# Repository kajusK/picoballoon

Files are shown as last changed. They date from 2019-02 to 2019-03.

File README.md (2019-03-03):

Picoballoon challange 2019, team deadbadger probe
-------------------------------------------------

This repo contains source codes and hw design of the picoballoon probe designed
for https://www.hvezdarna.cz/?p=7694.

Due to the lack of free time, the pcb is very suboptimal as I needed single sided
board with wider traces for diy manufacturing process (made it few days before the
launch, didn't have enough time to send it to a pcb house).

The circuit contains:
- MCU stm32f070
- GPS u-blox max-m8
- Lora module HPD13
- Analog thermometer
- Digital pressure sensor MS5607 (failed to make it working before start - getting nack all the time)
- Solar panel that charges the supercap (wanted bare cells from china, but delivery time was too long, used one quite heavy panel from my junk box)
- 3.3 V boost switching power supply with startup circuit (starts around 2,5 V)

The software is quite simplified too. The Lmic library takes care of the LoRa
communications. Minmea handles processing nmea messages from gps. For future
reference, the libopencm3 is not the best option when dealing with stm32f0
family, I've had serious issues with rtc wakeup timer and failed
to wake up from deep sleep on rtc events anyway...

The code does following:
- Initialize peripherals
- Send LoRa join request
- Try to get the gps position
- After gps fix or timeout, send data over the LoRa connection and shutdown

Sending period depends on amount of sunlight (solar cell current) and supercap
capacity.

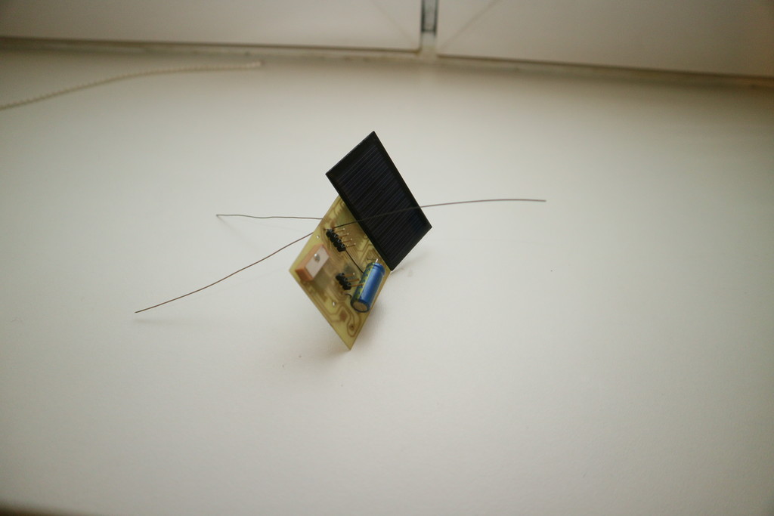
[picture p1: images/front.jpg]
Front

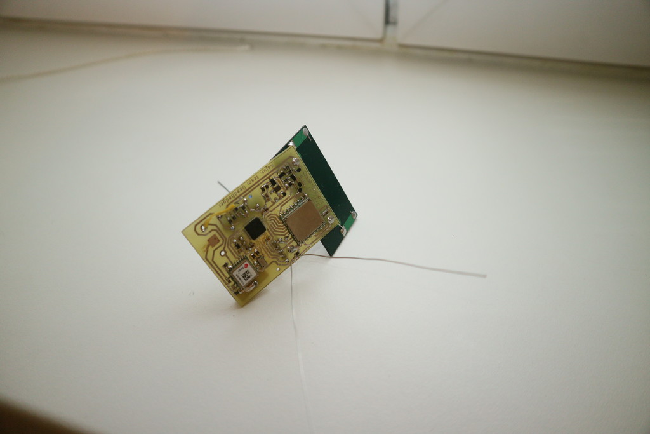
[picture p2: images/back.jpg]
Back


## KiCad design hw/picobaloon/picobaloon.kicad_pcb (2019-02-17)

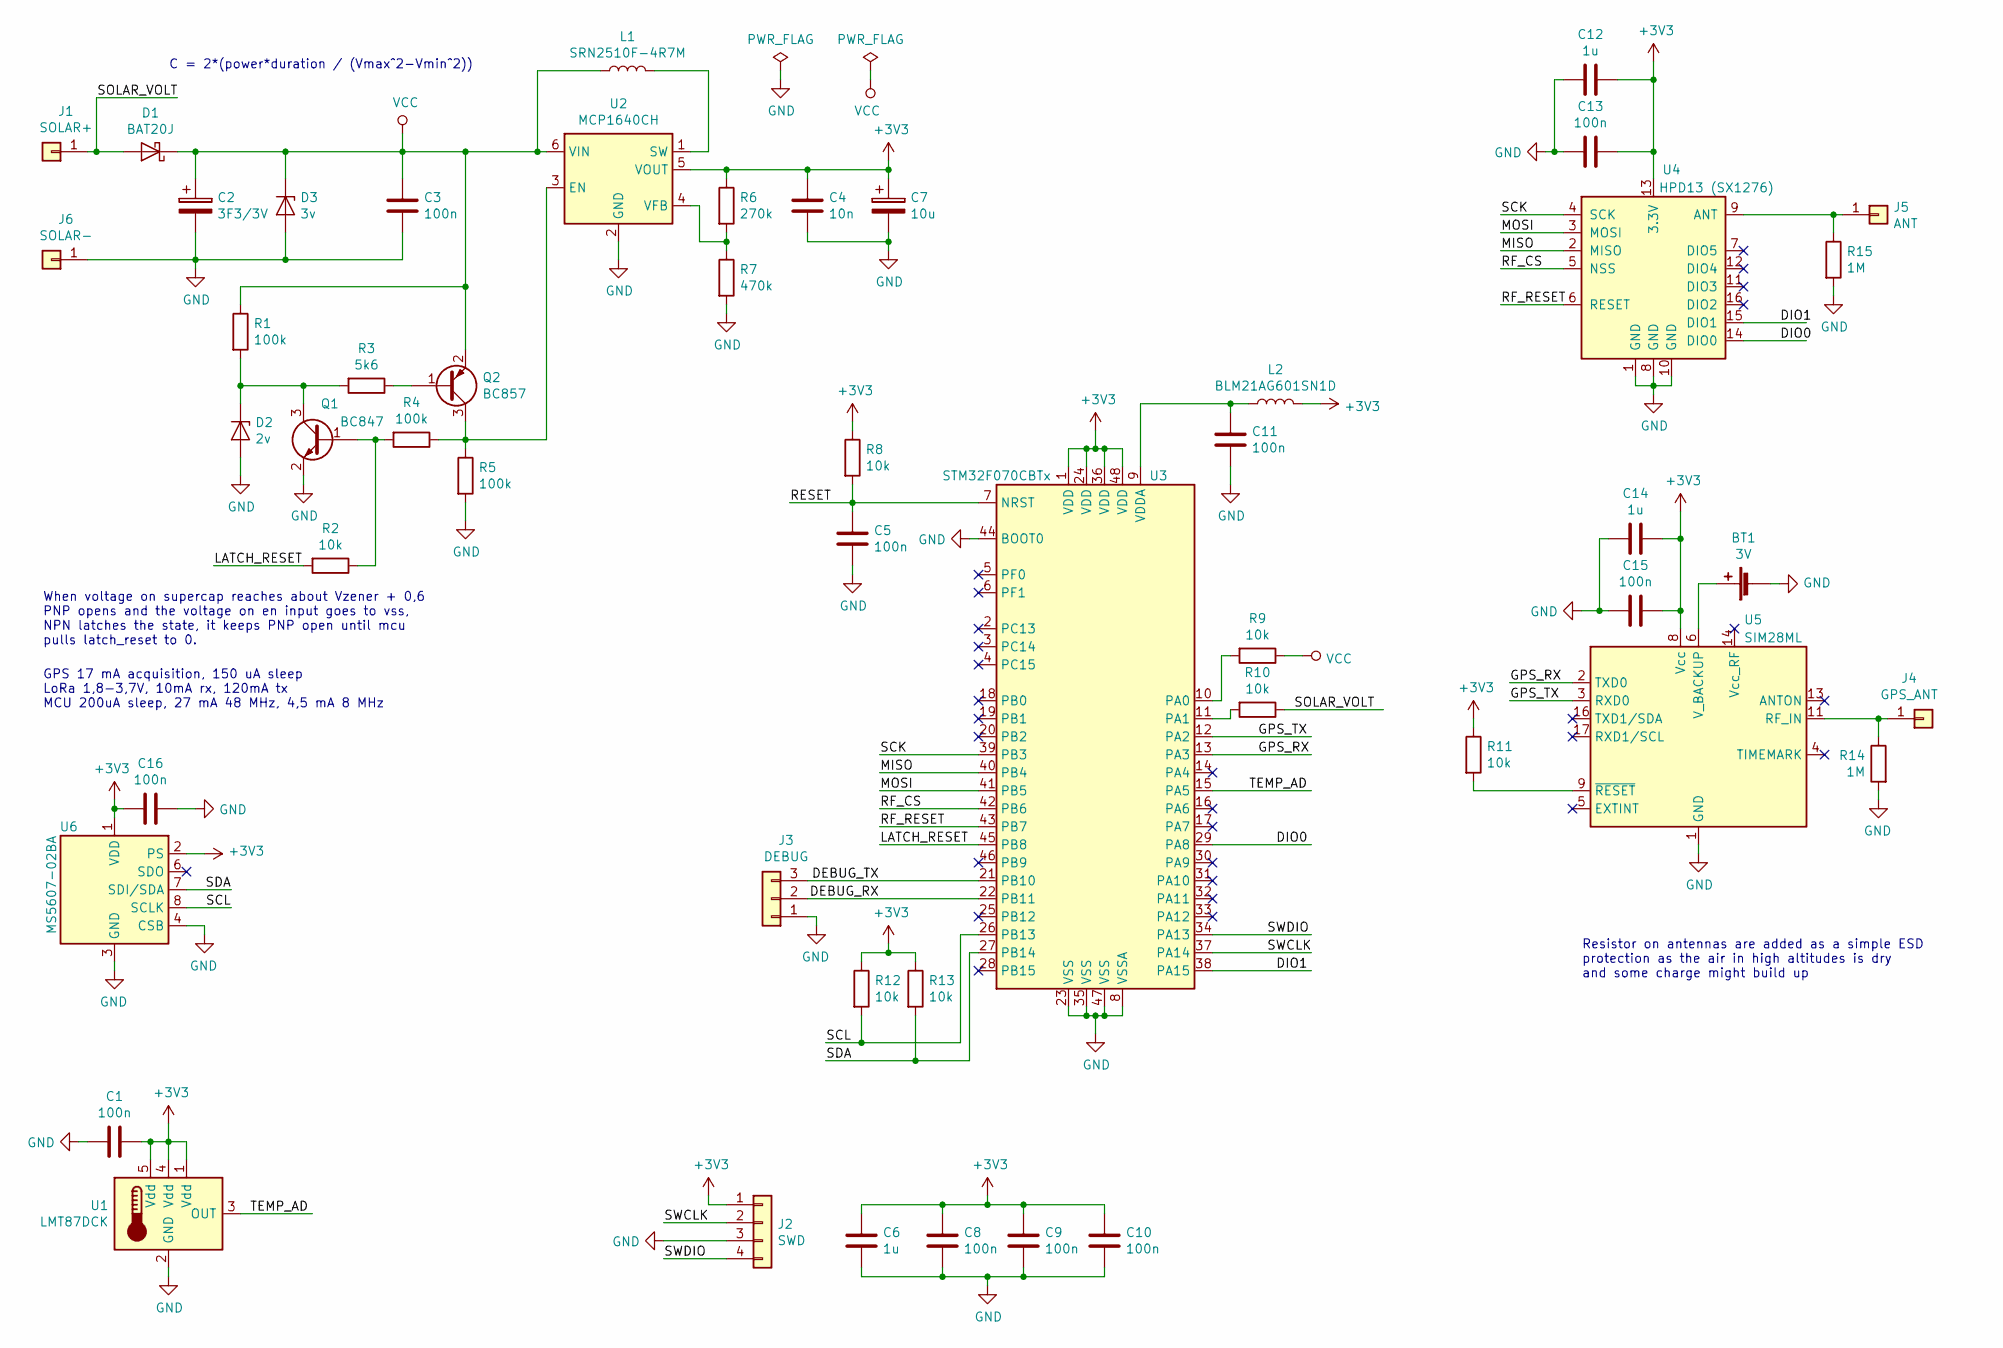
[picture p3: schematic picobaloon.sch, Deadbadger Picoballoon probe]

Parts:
BT1: 3V; BatteryHolder_Keystone_3001_1x12mm
C1, C3, C5, C8, C9, C10, C11, C13, C15, C16: 100n; C_0805_2012Metric
C2: 3F3/3V; CP_Radial_D8.0mm_P3.50mm
C4: 10n; C_0805_2012Metric
C6, C12, C14: 1u; C_0805_2012Metric
C7: 10u; C_0805_2012Metric
D1: BAT20J; D_SOD-323
D2: 2v; D_SOD-323
D3: 3v; D_SOD-323
J1: SOLAR+; SolderWirePad_1x01_Drill1.2mm
J2: SWD; PinHeader_1x04_P2.54mm_Vertical
J3: DEBUG; PinHeader_1x03_P2.54mm_Vertical
J4: GPS_ANT; SolderWirePad_1x01_Drill1.2mm
J5: ANT; SolderWirePad_1x01_Drill1.2mm
J6: SOLAR-; SolderWirePad_1x01_Drill1.2mm
L1: SRN2510F-4R7M; L_Abracon_ASPI-3012S
L2: BLM21AG601SN1D; L_0805_2012Metric
Q1: BC847; SOT-23
Q2: BC857; SOT-23
R1, R4, R5: 100k; R_0805_2012Metric
R2, R8, R9, R10, R11, R12, R13: 10k; R_0805_2012Metric
R3: 5k6; R_0805_2012Metric
R6: 270k; R_0805_2012Metric
R7: 470k; R_0805_2012Metric
R14, R15: 1M; R_0805_2012Metric
U1: LMT87DCK; SOT-353_SC-70-5
U2: MCP1640CH; SOT-23-6
U3: STM32F070CBTx; LQFP-48_7x7mm_P0.5mm
U4: HPD13 (SX1276); HOPERF_RFM9XW_SMD
U5: SIM28ML
U6: MS5607-02BA; LGA-8_3x5mm_P1.25mm

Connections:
+3V3: C1.1, C4.1, C6.1, C7.1, C8.1, C9.1, C10.1, C12.1, C13.1, C14.1, C15.1, C16.1, J2.1, L2.2, R6.1, R8.1, R11.1, R12.1, R13.1, U1.1 (Vdd), U1.4 (Vdd), U1.5 (Vdd), U2.5 (VOUT), U3.1 (VDD), U3.24 (VDD), U3.36 (VDD), U3.48 (VDD), U4.13 (3.3V), U5.8 (Vcc), U6.1 (VDD), U6.2 (PS)
/DEBUG_RX: J3.2, U3.22 (PB11)
/DEBUG_TX: J3.3, U3.21 (PB10)
/DIO0: U3.29 (PA8), U4.14 (DIO0)
/DIO1: U3.38 (PA15), U4.15 (DIO1)
/GPS_RX: U3.13 (PA3), U5.2 (TXD0)
/GPS_TX: U3.12 (PA2), U5.3 (RXD0)
/LATCH_RESET: R2.2, U3.45 (PB8)
/MISO: U3.40 (PB4), U4.2 (MISO)
/MOSI: U3.41 (PB5), U4.3 (MOSI)
/RESET: C5.1, R8.2, U3.7 (NRST)
/RF_CS: U3.42 (PB6), U4.5 (NSS)
/RF_RESET: U3.43 (PB7), U4.6 (RESET)
/SCK: U3.39 (PB3), U4.4 (SCK)
/SCL: R12.2, U3.26 (PB13), U6.8 (SCLK)
/SDA: R13.2, U3.27 (PB14), U6.7 (SDI/SDA)
/SOLAR_VOLT: D1.2 (A), J1.1, R10.1
/SWCLK: J2.2, U3.37 (PA14)
/SWDIO: J2.4, U3.34 (PA13)
/TEMP_AD: U1.3 (OUT), U3.15 (PA5)
GND: BT1.2 (-), C1.2, C2.2, C3.2, C4.2, C5.2, C6.2, C7.2, C8.2, C9.2, C10.2, C11.2, C12.2, C13.2, C14.2, C15.2, C16.2, D2.2 (A), D3.2 (A), J2.3, J3.1, J6.1, Q1.2 (E), R5.2, R7.2, R14.2, R15.2, U1.2 (GND), U2.2 (GND), U3.8 (VSSA), U3.23 (VSS), U3.35 (VSS), U3.44 (BOOT0), U3.47 (VSS), U4.1 (GND), U4.8 (GND), U4.10 (GND), U5.1 (GND), U5.10 (GND), U5.12 (GND), U6.3 (GND), U6.4 (CSB), U6.5 (CSB)
unnamed: BT1.1 (+), U5.6 (V_BACKUP)
unnamed: C11.1, L2.1, U3.9 (VDDA)
unnamed: D2.1 (K), Q1.3 (C), R1.2, R3.2
unnamed: J4.1, R14.1, U5.11 (RF_IN)
unnamed: J5.1, R15.1, U4.9 (ANT)
unnamed: L1.2, U2.1 (SW)
unnamed: Q1.1 (B), R2.1, R4.2
unnamed: Q2.1 (B), R3.1
unnamed: Q2.3 (C), R4.1, R5.1, U2.3 (EN)
unnamed: R6.2, R7.1, U2.4 (VFB)
unnamed: R9.2, U3.10 (PA0)
unnamed: R10.2, U3.11 (PA1)
unnamed: R11.2, U5.9 (~RESET)
VCC: C2.1, C3.1, D1.1 (K), D3.1 (K), L1.1, Q2.2 (E), R1.1, R9.1, U2.6 (VIN)

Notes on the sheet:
C = 2*(power*duration / (Vmax^2-Vmin^2))
GPS 17 mA acquisition, 150 uA sleep LoRa 1,8-3,7V, 10mA rx, 120mA tx MCU 200uA sleep, 27 mA 48 MHz, 4,5 mA 8 MHz
When voltage on supercap reaches about Vzener + 0,6 PNP opens and the voltage on en input goes to vss, NPN latches the state, it keeps PNP open until mcu pulls latch_reset to 0.
Resistor on antennas are added as a simple ESD protection as the air in high altitudes is dry and some charge might build up

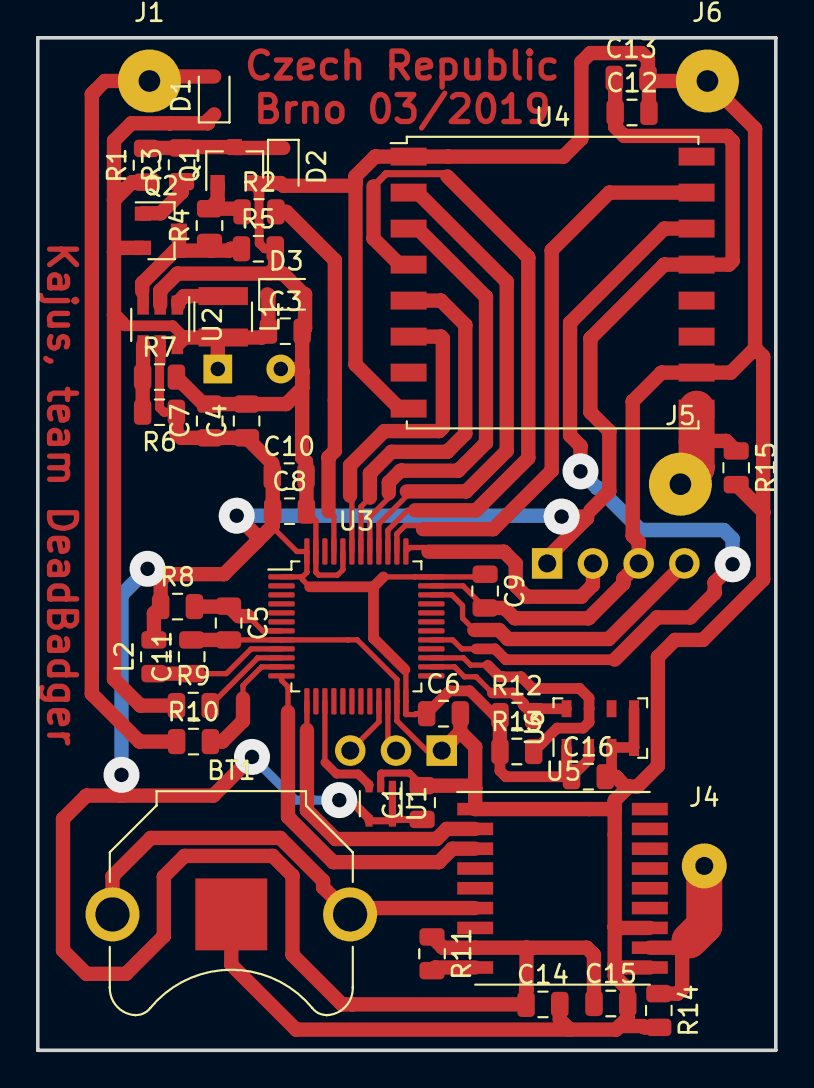
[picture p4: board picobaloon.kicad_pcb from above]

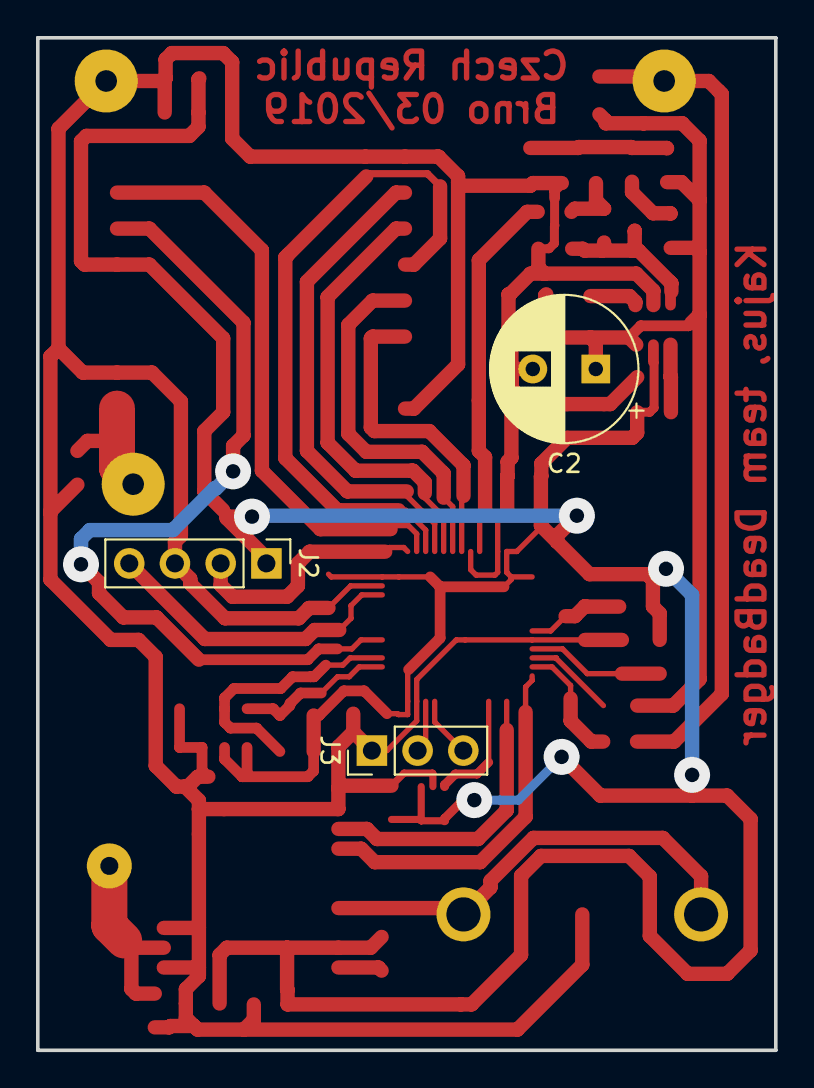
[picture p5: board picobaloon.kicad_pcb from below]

Board: 2 copper layers, 41.0 x 56.3 mm, 51 parts (3 on the bottom side), 35 nets.

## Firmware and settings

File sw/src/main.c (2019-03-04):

/*
 * Copyright (c) 2019 Jakub Kaderka
 *
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
 * THE SOFTWARE IS PROVIDED "AS IS", WITHOUT WARRANTY OF ANY KIND, EXPRESS OR
 * IMPLIED, INCLUDING BUT NOT LIMITED TO THE WARRANTIES OF MERCHANTABILITY,
 * FITNESS FOR A PARTICULAR PURPOSE AND NONINFRINGEMENT. IN NO EVENT SHALL THE
 * AUTHORS OR COPYRIGHT HOLDERS BE LIABLE FOR ANY CLAIM, DAMAGES OR OTHER
 * LIABILITY, WHETHER IN AN ACTION OF CONTRACT, TORT OR OTHERWISE, ARISING FROM,
 * OUT OF OR IN CONNECTION WITH THE SOFTWARE OR THE USE OR OTHER DEALINGS IN THE
 * SOFTWARE.
 */

#include <inttypes.h>
#include <stdio.h>
#include <libopencm3/stm32/rcc.h>
#include <libopencm3/stm32/gpio.h>

#include "drivers/wdg.h"
#include "drivers/systick.h"
#include "drivers/gps.h"
#include "drivers/adc.h"
#include "drivers/stdout.h"
#include "drivers/i2c.h"
#include "drivers/power.h"
#include "drivers/rtc.h"
#include "gps.h"
#include "sensors.h"
#include "lora.h"
#include "probe.h"
#include "main.h"

/**
 * Print out debug message containing all the sensors data
 */
static void Print_Debug(void)
{
    struct minmea_sentence_gga *frame;
    uint16_t cap_mv = Sensors_GetCapMv();
    uint16_t solar_mv = Sensors_GetSolarMv();
    uint16_t core_mv = Adcd_ReadVccMv();
    int16_t core_c = Adcd_ReadTempDegC();
    int8_t temp2 = Sensors_TempDegC();
    uint32_t pressure;
    int32_t temp;

    Sensors_PressurecMbar(&pressure, &temp);

    puts("\n\n-----------\nProbe debug:");
    printf("Capacitor: %d mV\n", cap_mv);
    printf("Solar cell: %d mV\n", solar_mv);
    printf("Core voltage: %d mV\n", core_mv);
    printf("Core temperature: %d C\n", core_c);
    printf("Pressure: %ld mbar\n", pressure / 100);
    printf("Temperature: %ld C\n", temp / 100);
    printf("Temperature sensor: %d C\n", temp2);

    if (!Gps_GotFix()) {
        puts("GPS fix: No\n----------");
        return;
    }

    frame = Gps_GetGga();
    printf("GPS fix:\nlat %f\n lon %f\n altitude %d\n",
        minmea_tocoord(&frame->latitude),
        minmea_tocoord(&frame->longitude),
        (int) (frame->altitude.value / frame->altitude.scale));
    puts("-------------\n");
}

/**
 * Set all gpio as inputs with pullup
 *
 * Avoids floating pins to reduce power consumption
 */
static void Sysi_GpioDefault(void)
{
    rcc_periph_clock_enable(RCC_GPIOA);
    rcc_periph_clock_enable(RCC_GPIOB);
    rcc_periph_clock_enable(RCC_GPIOC);
    rcc_periph_clock_enable(RCC_GPIOF);
    /* PA13 and 14 are swd */
    gpio_mode_setup(GPIOA, GPIO_MODE_INPUT, GPIO_PUPD_PULLUP, 0xffff & (~(0x03 << 13)));
    gpio_mode_setup(GPIOB, GPIO_MODE_INPUT, GPIO_PUPD_PULLUP, 0xffff);
    gpio_mode_setup(GPIOC, GPIO_MODE_INPUT, GPIO_PUPD_PULLUP, 0xffff);
    gpio_mode_setup(GPIOF, GPIO_MODE_INPUT, GPIO_PUPD_PULLUP, 0xffff);
}

static void Sysi_Init(void)
{
    Sysi_GpioDefault();

    Wdgd_Init();
    RTCd_Init();
    Stdoutd_Init();
    Systickd_Init();

    Adcd_Init();
    I2Cd_Init();

    GPSd_Init();
    Sensors_PinsInit();
}

void Sys_Sleep(uint32_t sleep_s)
{
    puts("flushing lora");
    while (!Lora_IsAllSent()) {
        Lora_Update();
        /* Wdg should be long enough for whole lora communication to avoid
         * being locked here */
    }
    puts("Going to sleep. Good night.");
    GPSd_SetPower(false);
    Lora_PowerOff();
    Adcd_Sleep();
    Sysi_GpioDefault();

    delay_ms(3000);
    Powerd_Sleep(sleep_s);
    Stdoutd_Init();

    /** Reinitialize all peripherals after sleep mode */
    Wdgd_Clear();
    Sysi_Init();
    puts("Woken up");
    Gps_FixClear();
    GPSd_SetPower(true);
    Adcd_Wakeup();
    Lora_PowerOn();
}

void Sys_Shutdown(void)
{
    GPSd_SetPower(false);
    Adcd_Sleep();
    puts("flushing lora");
    /* Wait for lora to send all remaining data */
    while (!Lora_IsAllSent()) {
        Lora_Update();
        /* Wdg should be long enough for whole lora communication to avoid
         * being locked here */
    }
    puts("Shutting down... Don't want do die yet, I'm too young!");
    Powerd_ShutDown();
}

int main(void)
{
    Sysi_Init();

    puts("-------------------------");
    puts("Brno Observatory and Planetarium Pico Balloon Challange 2019");
    puts("Team DeadBadger, Jakub Kaderka 2019");
    puts("-------------------------");

    GPSd_SetPower(true);
    GPSd_SetPowerSave();
    Sensors_PressureInit();
    Lora_Init();

    while (1) {
        Lora_Update();
        Adcd_UpdateVdda();
        Probe_Loop();
        Wdgd_Clear();
    }
}

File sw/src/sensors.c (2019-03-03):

/*
 * Copyright (c) 2019 Jakub Kaderka
 *
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
 * THE SOFTWARE IS PROVIDED "AS IS", WITHOUT WARRANTY OF ANY KIND, EXPRESS OR
 * IMPLIED, INCLUDING BUT NOT LIMITED TO THE WARRANTIES OF MERCHANTABILITY,
 * FITNESS FOR A PARTICULAR PURPOSE AND NONINFRINGEMENT. IN NO EVENT SHALL THE
 * AUTHORS OR COPYRIGHT HOLDERS BE LIABLE FOR ANY CLAIM, DAMAGES OR OTHER
 * LIABILITY, WHETHER IN AN ACTION OF CONTRACT, TORT OR OTHERWISE, ARISING FROM,
 * OUT OF OR IN CONNECTION WITH THE SOFTWARE OR THE USE OR OTHER DEALINGS IN THE
 * SOFTWARE.
 */

#include <stdio.h>
#include <stdlib.h>
#include "drivers/systick.h"
#include "drivers/adc.h"
#include "drivers/i2c.h"

#include "sensors.h"

#define AD_CHANNEL_SUPERCAP 0
#define AD_CHANNEL_SOLAR 1
#define AD_CHANNEL_TEMP 5

/** Time for pressure sensor conversion */
#define MS5607_CONVERT_MS 10
/** I2C address of the pressure sensor */
#define MS5607_ADDR 0x76

/** Pressure sensor commands */
#define MS5607_CMD_RESET 0x1e
#define MS5607_CMD_PROM 0xa0
#define MS5607_CMD_READ_ADC 0x00
#define MS5607_CMD_CONV_PRESS 0x48
#define MS5607_CMD_CONV_TEMP 0x58

static const int16_t lmt87_lookup[][2] = {
    {3277, -50},
    {3160, -40},
    {3030, -30},
    {2899, -20},
    {2767, -10},
    {2633, 0},
    {2365, 20},
    {2095, 40},
    {1819, 60},
    {1539, 80},
    {1257, 100},
};

static uint16_t ms5607_calib[6];

static bool Sensorsi_MS5607Cmd(uint8_t cmd, uint8_t *buf, uint8_t len)
{
    return I2Cd_Transceive(MS5607_ADDR, &cmd, 1, buf, len);
}

int32_t Sensors_TempDegC(void)
{
    int i;
    int16_t x1, x2;
    int16_t y1, y2;
    uint8_t size = sizeof(lmt87_lookup)/sizeof(lmt87_lookup[0]);
    uint16_t volt = Adcd_ReadMv(AD_CHANNEL_TEMP);

    for (i = 0; i < size; i++) {
        if (volt >= lmt87_lookup[i][0]) {
            break;
        }
    }

    if (i == 0) {
        i = 1;
    } else if (i == size) {
        i = size - 1;
    }

    x1 = lmt87_lookup[i-1][0];
    x2 = lmt87_lookup[i][0];
    y1 = lmt87_lookup[i-1][1];
    y2 = lmt87_lookup[i][1];

    return y1 + ((int32_t)(volt - x1)*(y2-y1))/(x2 - x1);
}

void Sensors_PressurecMbar(uint32_t *pressure, int32_t *temperature)
{
    uint32_t d2;
    uint32_t d1;
    int32_t temp, t2, dt;
    int64_t off, off2, sens, sens2;
    int32_t press;

    Sensorsi_MS5607Cmd(MS5607_CMD_CONV_TEMP, NULL, 0);
    delay_ms(MS5607_CONVERT_MS);
    Sensorsi_MS5607Cmd(MS5607_CMD_READ_ADC, (uint8_t *) &d2, 3);

    Sensorsi_MS5607Cmd(MS5607_CMD_CONV_PRESS, NULL, 0);
    delay_ms(MS5607_CONVERT_MS);
    Sensorsi_MS5607Cmd(MS5607_CMD_READ_ADC, (uint8_t *) &d1, 3);

    dt = d2 - (uint32_t)(ms5607_calib[4] << 8);
    temp = 2000 + (((int64_t) dt*ms5607_calib[5]) >> 23);

    /* Second order compensation */
    if (temp >= 2000) {
        t2 = 0;
        sens2 = 0;
        off2 = 0;
    } else {
        int64_t square = (temp-2000);
        square *= square;

        t2 = ((int64_t) dt * dt) >> 31;
        off2 = 61*(square >> 4);
        sens2 = 2*square;
        if (temp < -1500) {
            square = temp + 1500;
            square *= square;

            off2 += 15*square;
            sens2 += 8*square;
        }
    }

    off = ((int64_t)ms5607_calib[1] << 17) + (((int64_t)ms5607_calib[3]*dt) >> 6);
    sens = ((int64_t)ms5607_calib[0] << 16) + (((int64_t)ms5607_calib[2]*dt) >> 7);

    temp = temp - t2;
    off = off - off2;
    sens = sens - sens2;
    press = (((d1*sens) >> 21) - off) >> 15;

    *pressure = press;
    *temperature = temp;
}

uint16_t Sensors_GetSolarMv(void)
{
    return Adcd_ReadMv(AD_CHANNEL_SOLAR);
}

uint16_t Sensors_GetCapMv(void)
{
    return Adcd_ReadMv(AD_CHANNEL_SUPERCAP);
}

void Sensors_PinsInit(void)
{
    Adcd_SetAnalog(GPIOA, 1 << AD_CHANNEL_SUPERCAP);
    Adcd_SetAnalog(GPIOA, 1 << AD_CHANNEL_SOLAR);
    Adcd_SetAnalog(GPIOA, 1 << AD_CHANNEL_TEMP);
}

void Sensors_PressureInit(void)
{
    bool ret;

    Sensorsi_MS5607Cmd(MS5607_CMD_RESET, NULL, 0);

    /** Read calibration data for pressure calculations */
    for (int i = 0; i < 6; i++) {
        ret = Sensorsi_MS5607Cmd(MS5607_CMD_PROM + (i << 1),
                (uint8_t *) &ms5607_calib[i], 2);
        if (ret == false) {
            puts("Failed to read pressure table");
            return;
        }
    }
}

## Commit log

2019-02-06 Hw revision v0.1
    [picobaloon.kicad_pcb, picobaloon.sch]
2019-02-06 HW revision 2 - added pressure sensor
    [picobaloon.kicad_pcb, picobaloon.sch]
2019-02-06 HW revision 3. Added resistors for simple esd protection
    [picobaloon.kicad_pcb, picobaloon.sch]
2019-02-17 Updated schematic to match the final symbol in the official repo
    [picobaloon.kicad_pcb, picobaloon.sch]
2019-02-17 Moved few files to drivers
2019-02-17 Added sensors measurements
2019-02-17 Fixed lora names and include
    [main.c]
2019-02-17 Added basics of probe logic
2019-02-17 Added power control to gps driver
2019-02-19 Enabled adc clock
2019-02-19 Fixed uart output clock
    [stdout.c]
2019-02-19 Used modified i2c transmit function from library, original gets to infinite loop on nack
2019-02-19 Fixed gps driver transmit data
    [gps.c]
2019-02-20 Fixed lmic hal (there was a bug in spi library)
    [lmic_hal.c]
2019-02-22 Fixed lmic driver (timing, interrupts,...)
    [lmic_hal.c]
2019-02-22 Fixed lora printouts, added lmic error setup to init
2019-02-22 Fixed bug in exti reading
    [lmic_hal.c]
2019-02-22 Removed print on gps
2019-02-24 Added clearing of the gps fix
    [gps.c]
2019-02-24 Moved probe logic to it's own file
2019-02-24 Fixed mcu type and enable printf for floats
2019-03-03 Reset pressure sensor before initializing
    [sensors.c]
2019-03-03 Updated critical voltage level for sending data
2019-03-04 Added some powersaving before sending lora
